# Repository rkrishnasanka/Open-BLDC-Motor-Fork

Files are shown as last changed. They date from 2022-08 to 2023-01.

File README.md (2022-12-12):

## Custom ESC Hardware

This project contains the KiCAD design files for the custom ESC PCB.
The project was designed with KiCAD Version 6.0.6 and should be able to be edited this way.

Any non standard components are located in the `Additional_Components` folder. The `bom` folder contains an HTML file generated by the iBOM plugin with the layout and placement of all components.

The `ir2130_driver` folder was a first idea for the hardware with a different driver IC which was abandoned. It is kept for documentation purposes.

The git tag `evaluation_board` contains the first produced version of this board in a bigger formfactor with additional debugging pads.

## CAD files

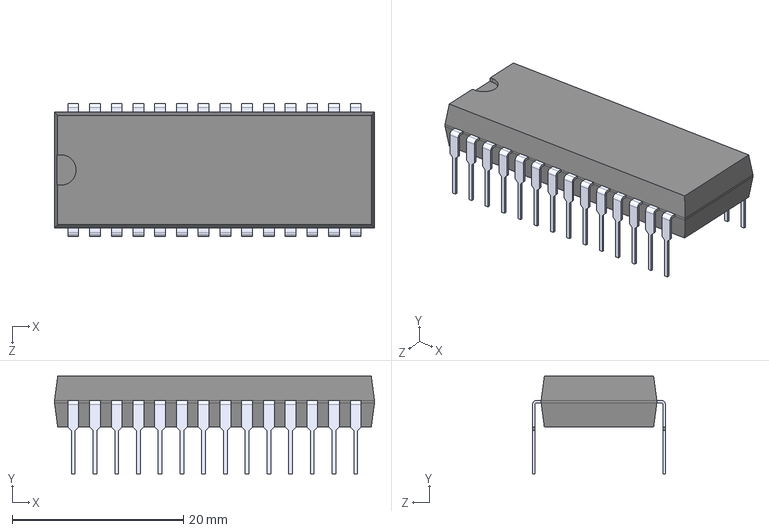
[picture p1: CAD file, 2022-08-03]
KiCAD/ir2130_driver/Additional_Components/IR2130.step
37.4 x 11.4 x 15.5 mm

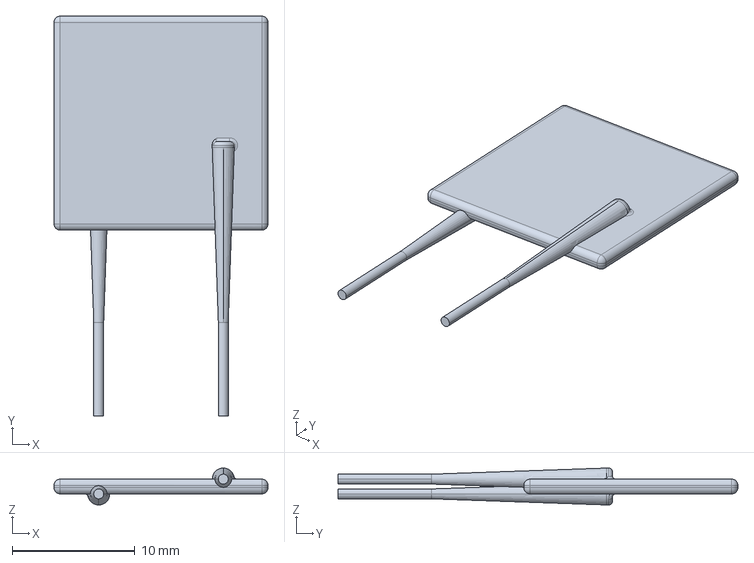
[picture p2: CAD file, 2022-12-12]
KiCAD/simplefoc_schematic/Additional_Components/mf-r500.stp
17.4 x 32.5 x 3.00 mm

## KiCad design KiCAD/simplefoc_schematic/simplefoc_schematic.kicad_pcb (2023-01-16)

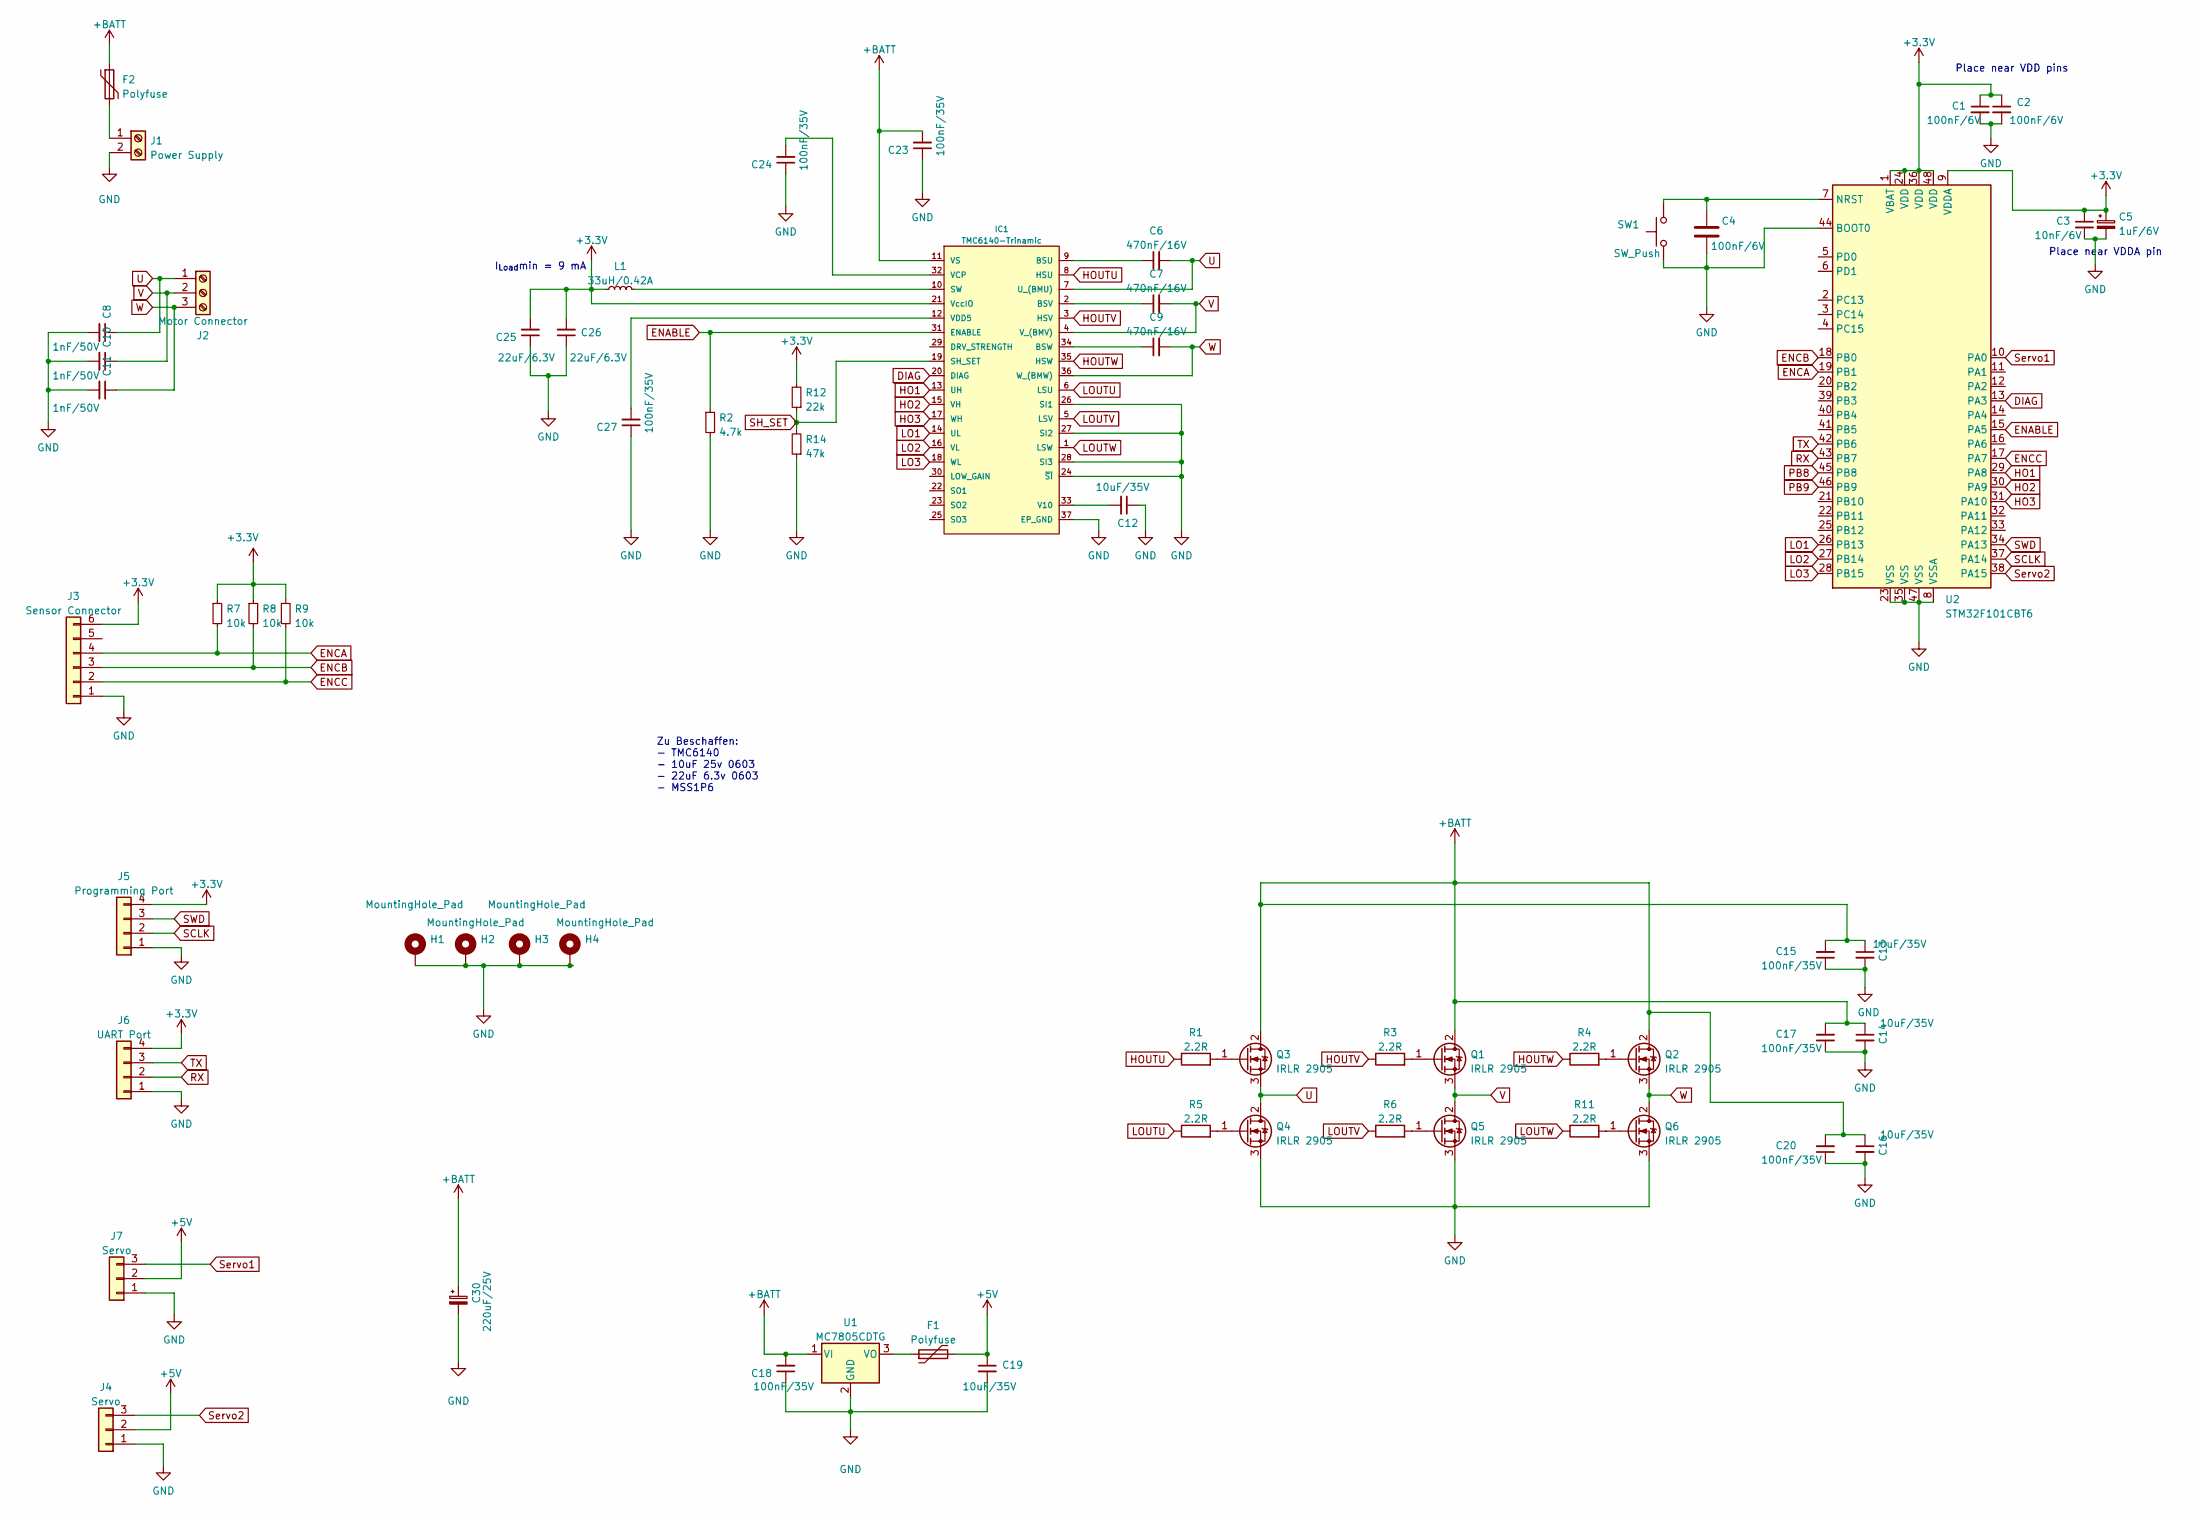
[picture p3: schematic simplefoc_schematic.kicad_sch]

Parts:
C1, C2, C4: 100nF/6V; C_0603_1608Metric
C3: 10nF/6V; C_0603_1608Metric
C5: 1uF/6V; C_0603_1608Metric
C6, C7, C9: 470nF/16V; C_0603_1608Metric
C8, C10, C11: 1nF/50V; C_0603_1608Metric
C12, C13, C14, C16, C19: 10uF/35V; C_0603_1608Metric
C15, C17, C18, C20, C23, C24, C27: 100nF/35V; C_0603_1608Metric
C25, C26: 22uF/6.3V; C_0603_1608Metric
C30: 220uF/25V; CP_Elec_8x10
F1: Polyfuse; Fuse_0603_1608Metric_Pad1.05x0.95mm_HandSolder
F2: Polyfuse; Fuse_2920_7451Metric_Pad2.10x5.45mm_HandSolder
H1, H2, H3, H4: MountingHole_Pad; MountingHole_2.2mm_M2_DIN965_Pad
IC1: TMC6140-Trinamic; QFN-36-1EP_5x6mm_P0.5mm_EP3.6x4.1mm
J1: Power Supply; TerminalBlock_Phoenix_MKDS-1,5-2_1x02_P5.00mm_Horizontal
J2: Motor Connector; TerminalBlock_Phoenix_MKDS-1,5-3_1x03_P5.00mm_Horizontal
J3: Sensor Connector; JST_ZH_B6B-ZR_1x06_P1.50mm_Vertical
J4, J7: Servo; PinSocket_1x03_P2.54mm_Vertical
J5: Programming Port; PinHeader_1x04_P2.54mm_Vertical
J6: UART Port; JST_XH_B4B-XH-A_1x04_P2.50mm_Vertical
L1: 33uH/0.42A; L_Fastron_1212_FPS
Q1, Q2, Q3, Q4, Q5, Q6: IRLR 2905; TO-252-2
R1, R3, R4, R5, R6, R11: 2.2R; R_0603_1608Metric
R2: 4.7k; R_0603_1608Metric
R7, R8, R9: 10k; R_0603_1608Metric
R12: 22k; R_0603_1608Metric
R14: 47k; R_0603_1608Metric
SW1: SW_Push; SW_Push_SPST_Wuerth_434121043816
U1: MC7805CDTG; TO-252-2
U2: STM32F101CBT6; LQFP-48_7x7mm_P0.5mm

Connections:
+3.3V: C1.1, C2.1, C3.1, C5.1, C25.2, C26.2, IC1.21 (VccIO), J3.6, J5.4, J6.4, L1.1, R7.1, R8.1, R9.1, R12.2, U2.1 (VBAT), U2.9 (VDDA), U2.24 (VDD), U2.36 (VDD), U2.48 (VDD)
+5V: C19.1, F1.2, J4.2, J7.2
+BATT: C13.1, C14.1, C15.2, C16.1, C17.2, C18.2, C20.2, C23.2, C30.1, F2.1, IC1.11 (VS), Q1.2 (D), Q2.2 (D), Q3.2 (D), U1.1 (VI)
DIAG: IC1.20 (DIAG), U2.13 (PA3)
ENABLE: IC1.31 (ENABLE), R2.1, U2.15 (PA5)
ENCA: J3.4, R7.2, U2.19 (PB1)
ENCB: J3.3, R8.2, U2.18 (PB0)
ENCC: J3.2, R9.2, U2.17 (PA7)
GND: C1.2, C2.2, C3.2, C4.2, C5.2, C8.2, C10.2, C11.2, C12.1, C13.2, C14.2, C15.1, C16.2, C17.1, C18.1, C19.2, C20.1, C23.1, C24.1, C25.1, C26.1, C27.1, C30.2, H1.1, H2.1, H3.1, H4.1, IC1.24 (~SI), IC1.26 (SI1), IC1.27 (SI2), IC1.28 (SI3), IC1.37 (EP_GND), J1.2, J3.1, J4.1, J5.1, J6.1, J7.1, Q4.3 (S), Q5.3 (S), Q6.3 (S), R2.2, R14.1, SW1.1, U1.2 (GND), U2.8 (VSSA), U2.23 (VSS), U2.35 (VSS), U2.44 (BOOT0), U2.47 (VSS)
HO1: IC1.13 (UH), U2.29 (PA8)
HO2: IC1.15 (VH), U2.30 (PA9)
HO3: IC1.17 (WH), U2.31 (PA10)
HOUTU: IC1.8 (HSU), R1.1
HOUTV: IC1.3 (HSV), R3.1
HOUTW: IC1.35 (HSW), R4.1
LO1: IC1.14 (UL), U2.26 (PB13)
LO2: IC1.16 (VL), U2.27 (PB14)
LO3: IC1.18 (WL), U2.28 (PB15)
LOUTU: IC1.6 (LSU), R5.1
LOUTV: IC1.5 (LSV), R6.1
LOUTW: IC1.1 (LSW), R11.1
unnamed: C4.1, SW1.2, U2.7 (NRST)
unnamed: C6.1, IC1.9 (BSU)
unnamed: C7.1, IC1.2 (BSV)
unnamed: C9.1, IC1.34 (BSW)
unnamed: C12.2, IC1.33 (V10)
unnamed: C24.2, IC1.32 (VCP)
unnamed: C27.2, IC1.12 (VDD5)
unnamed: IC1.10 (SW), L1.2
unnamed: F2.2, J1.1
unnamed: Q1.1 (G), R3.2
unnamed: Q2.1 (G), R4.2
unnamed: Q3.1 (G), R1.2
unnamed: Q4.1 (G), R5.2
unnamed: Q5.1 (G), R6.2
unnamed: Q6.1 (G), R11.2
unnamed: F1.1, U1.3 (VO)
PB8: U2.45 (PB8)
PB9: U2.46 (PB9)
RX: J6.2, U2.43 (PB7)
SCLK: J5.2, U2.37 (PA14)
SH_SET: IC1.19 (SH_SET), R12.1, R14.2
SWD: J5.3, U2.34 (PA13)
Servo1: J7.3, U2.10 (PA0)
Servo2: J4.3, U2.38 (PA15)
TX: J6.3, U2.42 (PB6)
U: C6.2, C8.1, IC1.7 (U_(BMU)), J2.1, Q3.3 (S), Q4.2 (D)
V: C7.2, C10.1, IC1.4 (V_(BMV)), J2.2, Q1.3 (S), Q5.2 (D)
W: C9.2, C11.1, IC1.36 (W_(BMW)), J2.3, Q2.3 (S), Q6.2 (D)

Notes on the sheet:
Place near VDDA pin
I_{Load}min = 9 mA
Zu Beschaffen: - TMC6140 - 10uF 25v 0603 - 22uF 6.3v 0603 - MSS1P6
Place near VDD pins

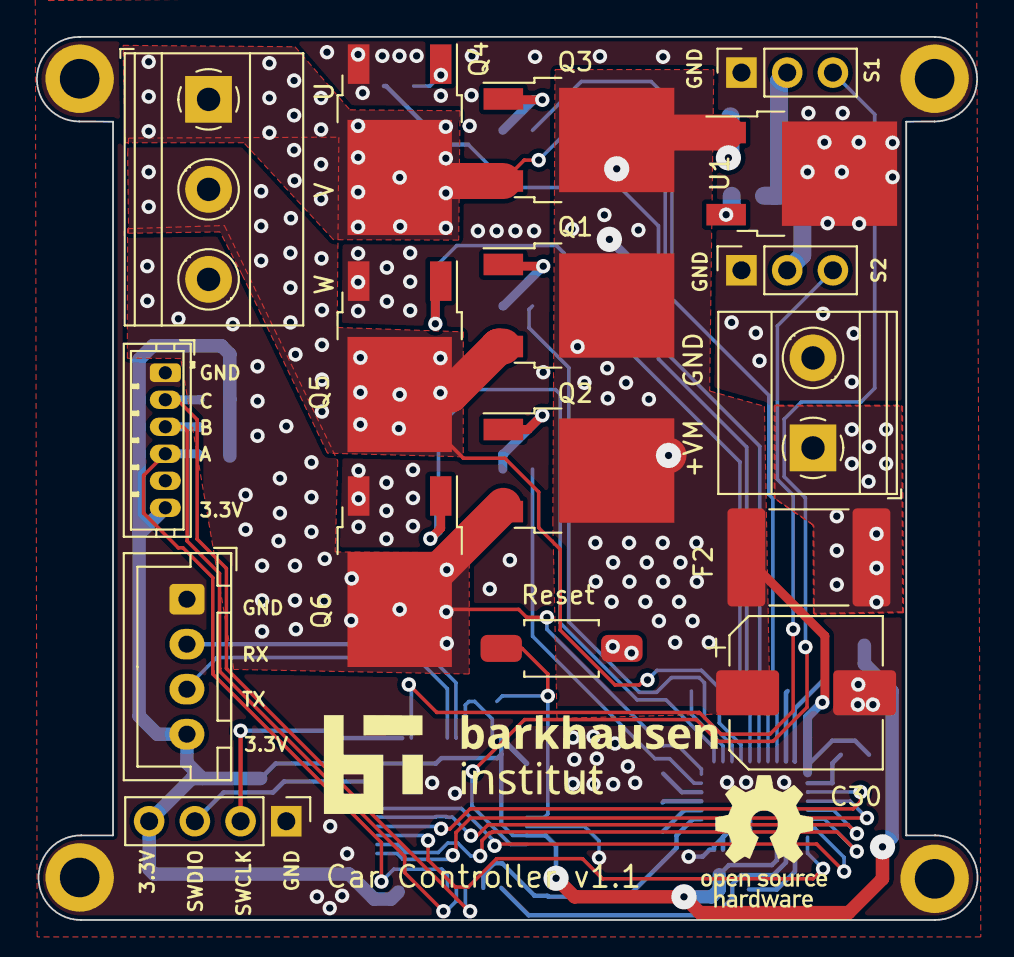
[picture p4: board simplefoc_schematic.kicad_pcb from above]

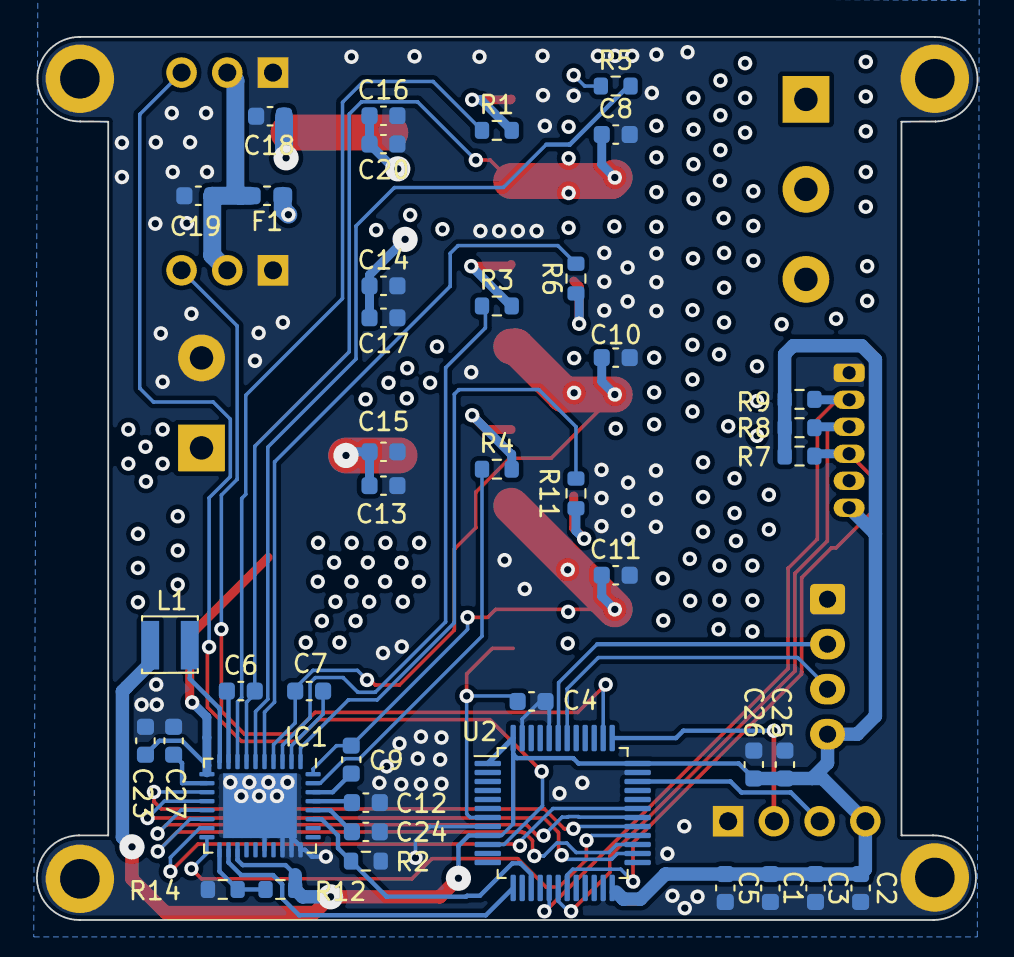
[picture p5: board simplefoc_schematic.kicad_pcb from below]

Board: 4 copper layers, 52.3 x 49.1 mm, 62 parts (41 on the bottom side), 47 nets.

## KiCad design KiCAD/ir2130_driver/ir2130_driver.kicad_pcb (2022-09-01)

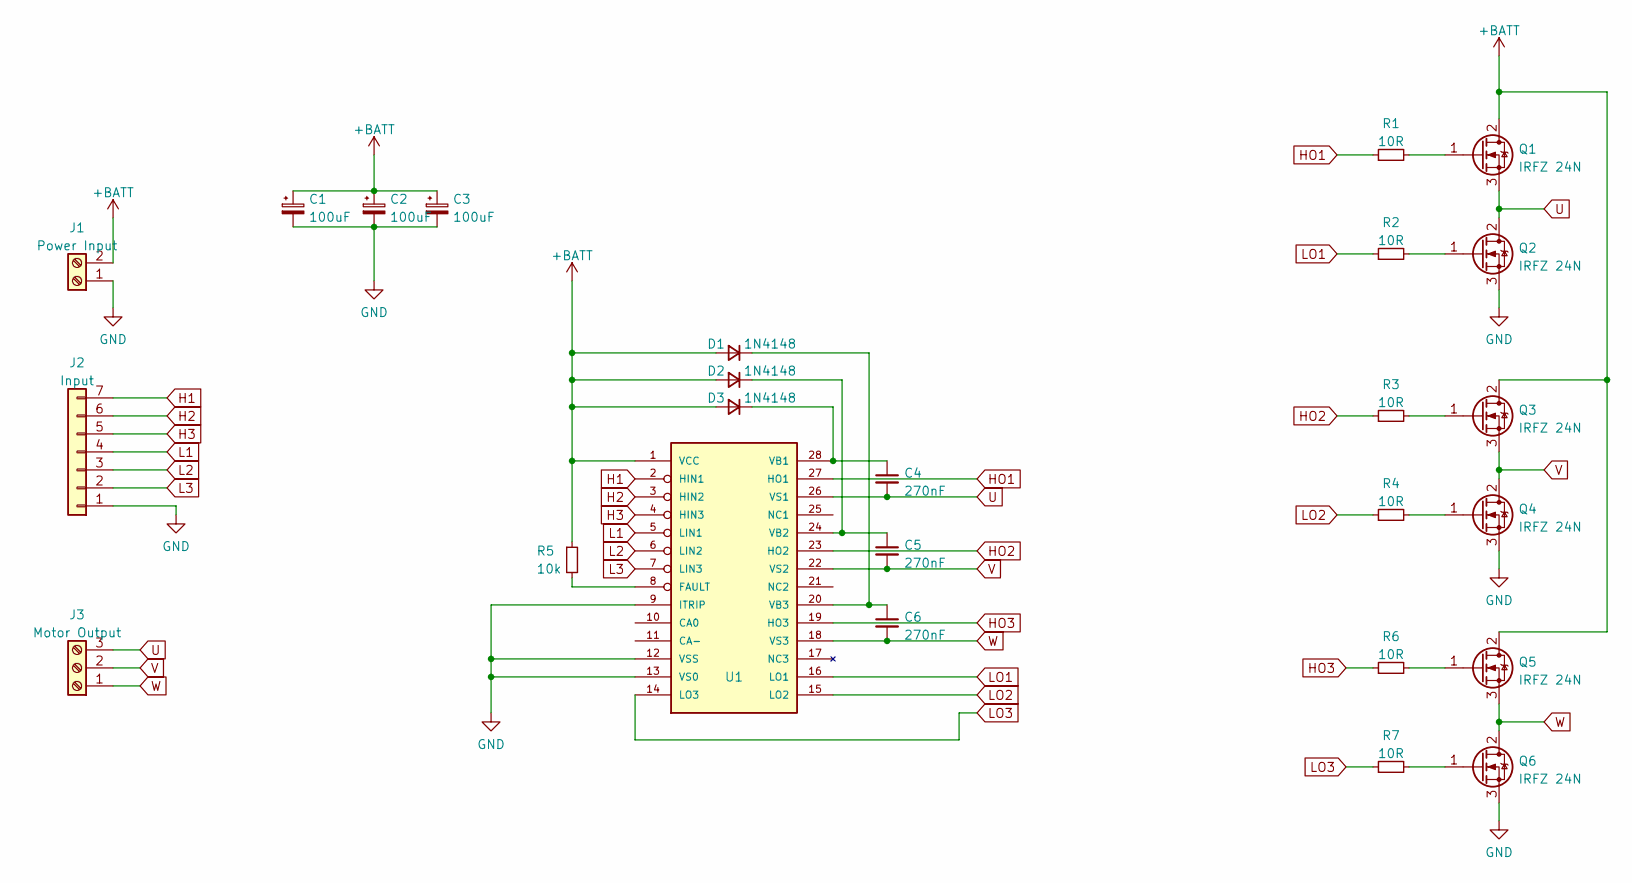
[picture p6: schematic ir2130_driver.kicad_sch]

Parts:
C1, C2, C3: 100uF; CP_Radial_D8.0mm_P2.50mm
C4, C5, C6: 270nF; CP_Radial_Tantal_D4.5mm_P2.50mm
D1, D2, D3: 1N4148; D_5W_P10.16mm_Horizontal
J1: Power Input; TerminalBlock_bornier-2_P5.08mm
J2: Input; PinHeader_1x07_P2.54mm_Vertical
J3: Motor Output; TerminalBlock_Altech_AK300-3_P5.00mm
Q1, Q2, Q3, Q4, Q5, Q6: IRFZ 24N; TO-220-3_Vertical
R1, R2, R3, R4, R6, R7: 10R; R_Axial_DIN0204_L3.6mm_D1.6mm_P5.08mm_Horizontal
R5: 10k; R_Axial_DIN0204_L3.6mm_D1.6mm_P5.08mm_Horizontal
U1: IR2130; DIP-28_W15.24mm_LongPads

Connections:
+BATT: C1.1, C2.1, C3.1, D1.2 (A), D2.2 (A), D3.2 (A), J1.2, Q1.2 (D), Q3.2 (D), Q5.2 (D), R5.1, U1.1 (VCC)
GND: C1.2, C2.2, C3.2, J1.1, J2.1, Q2.3 (S), Q4.3 (S), Q6.3 (S), U1.9 (ITRIP), U1.12 (VSS), U1.13 (VS0)
H1: J2.7, U1.2 (HIN1)
H2: J2.6, U1.3 (HIN2)
H3: J2.5, U1.4 (HIN3)
HO1: R1.1, U1.27 (HO1)
HO2: R3.1, U1.23 (HO2)
HO3: R6.1, U1.19 (HO3)
L1: J2.4, U1.5 (LIN1)
L2: J2.3, U1.6 (LIN2)
L3: J2.2, U1.7 (LIN3)
LO1: R2.1, U1.16 (LO1)
LO2: R4.1, U1.15 (LO2)
LO3: R7.1, U1.14 (LO3)
unnamed: C4.1, D3.1 (K), U1.28 (VB1)
unnamed: C5.1, D2.1 (K), U1.24 (VB2)
unnamed: C6.1, D1.1 (K), U1.20 (VB3)
unnamed: Q1.1 (G), R1.2
unnamed: Q2.1 (G), R2.2
unnamed: Q3.1 (G), R3.2
unnamed: Q4.1 (G), R4.2
unnamed: Q5.1 (G), R6.2
unnamed: Q6.1 (G), R7.2
unnamed: R5.2, U1.8 (FAULT)
U: C4.2, J3.3, Q1.3 (S), Q2.2 (D), U1.26 (VS1)
V: C5.2, J3.2, Q3.3 (S), Q4.2 (D), U1.22 (VS2)
W: C6.2, J3.1, Q5.3 (S), Q6.2 (D), U1.18 (VS3)

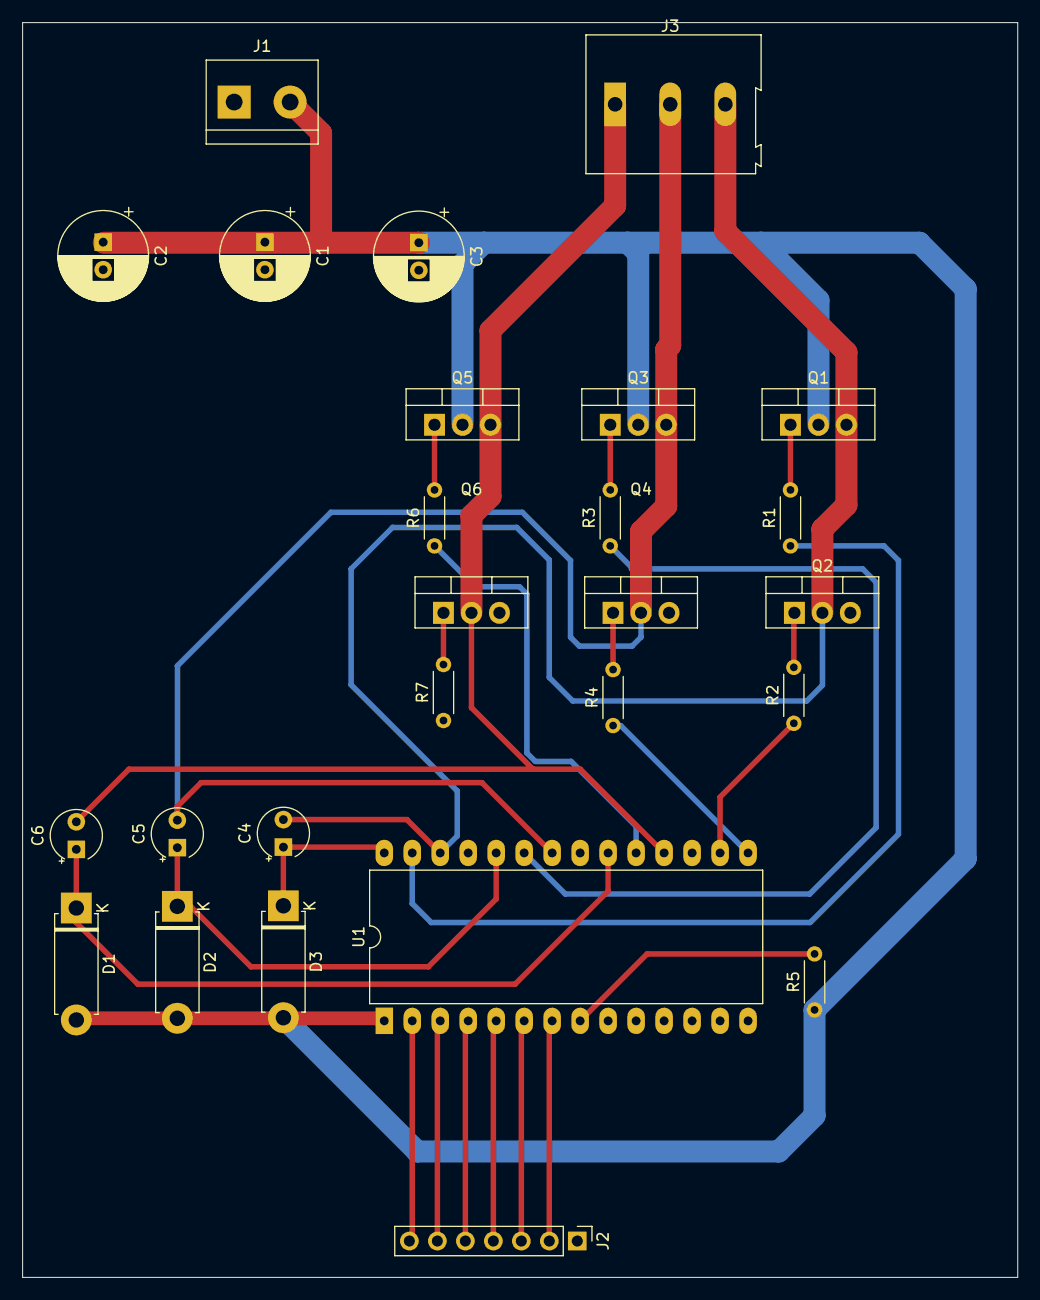
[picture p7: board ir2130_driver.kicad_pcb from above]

Board: 2 copper layers, 90.3 x 113.9 mm, 26 parts (0 on the bottom side), 27 nets.

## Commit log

2022-08-03 Added additional project for the test board of the ir2130 driver
    [IR2130.step, ir2130_driver.kicad_pcb, ir2130_driver.kicad_sch]
2022-08-03 Added PCB file for the IR2130 test board
    [ir2130_driver.kicad_pcb, ir2130_driver.kicad_sch]
2022-09-01 Added a standalone schematic for the STM32 part Moved from ir2130 driver to the TMC6140
    [ir2130_driver.kicad_pcb, ir2130_driver.kicad_sch, simplefoc_schematic.kicad_pcb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]
2022-09-06 Finalized schematic and component selection for acquisition from distributor
    [simplefoc_schematic.kicad_pcb, simplefoc_schematic.kicad_sch]
2022-09-29 Removed unused components and replaced some components with smaller ones
    [simplefoc_schematic.kicad_pcb, simplefoc_schematic.kicad_sch]
2022-09-30 Created first board layout for test board
    [simplefoc_schematic.kicad_pcb, simplefoc_schematic.kicad_sch]
2022-10-04 Minor changes to power tracks
    [simplefoc_schematic.kicad_pcb, simplefoc_schematic.kicad_sch]
2022-11-10 First design of the final small PCB
    [simplefoc_schematic.kicad_pcb, simplefoc_schematic.kicad_sch]
2022-11-14 Small changes to silk screen layout
    [simplefoc_schematic.kicad_pcb]
2022-11-21 Added second servo connection and fuse for servo
    [simplefoc_schematic.kicad_pcb, simplefoc_schematic.kicad_sch]
2022-11-21 Added polyfuse to battery input
    [simplefoc_schematic.kicad_pcb, simplefoc_schematic.kicad_sch]
2022-12-12 Final production version
    [mf-r500.stp]
2022-12-12 Removed the unused stm32_standalone project
    [stm32_standalone.kicad_pcb, stm32_standalone.kicad_sch]
2023-01-16 Change to 4 Layer PCB with better grounding
    [simplefoc_schematic.kicad_pcb]
